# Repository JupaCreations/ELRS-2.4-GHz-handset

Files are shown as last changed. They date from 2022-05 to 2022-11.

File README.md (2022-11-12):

ELRS-2.4-GHz 2 channel CAR TX handset.



This project is a rework of the ergonomic handset which can be found here.

https://www.thingiverse.com/thing:4868117

I reworked the upper and lower cover to make it comply to the needs of a simple 2 channel CAR TX handset with EXPRESSLRS as carrier.

All switches are removed.

The original Jumper T-Lite hall gimbals are placed in a way that they can be adjusted in an angle that comforts the movement of the thumb.

Two screws accesable from the top of the transmitter can loosend or fastend at each gimbal to put it in a desired angled position.
There are two versions of gimbal clamps as Jumper redesigned the housing of the gimbals I found out.
"T-lite TX gimbal retainer V2" is for the gimbal versions that can not be clamped at the edges with the "T-lite TX gimbal retainer" version.

I put M3 thread in the mounting holes of the gimbals. Drill a 2.5 mm drill through them first than use a 3mm thread tapping tool with care.
The V2 version gimbal brackets are attached to the gimbal mounting holes with M3x8 mm screws.
The brackets are clamped down with a retainer that has a M3 nut pressed in, in combination with M3x20mm screws. 

As this is a 2 channel application the left gimbal is for throttle and the right gimbal for steering.
With the "T-lite TX gimbal blocker" you can block the up/down motion in the not used direction of the gimbal.

For the ELRS part a DIY 2.4 GHz SX1280 with special PCB is used. When you use a Jumper T-lite V2 ELRS version as donor transnmitter this extra board is obsolete.

PCB design https://oshwlab.com/jyesmith/expresslrs-jumper-t-lite

Video 1 https://www.youtube.com/watch?v=8L0xCDgLQ8s

Video 2 https://www.youtube.com/watch?v=rfa2Ir5jLuc

The upper and lower cover are printed in PLA.
The lower cover has 4 inserts fitted with the size of 4.2 x 5 mm for M3 to secure the upper with the lower cover with M3x16mm hexagon screws.

The battery is a single 18650 3.3 volt cell.

The original Jumper T-Lite electronics are taken from a new handset and fitted with the original (4) screws in the upper cover.
The 4 wire cable from the gimbals to the mainboard might be to short in some cases and need a longer version as the handset is wider.

The receiver is a Happy Model EP2 receiver which is mounted on a DIY carrier board with a 5 volt regulator and the servo pins.
There are pins available for 2 channels (throttle and steering) and for the timing transponder if you use it for racing events.
Alternatively you can also use this receiver.
https://www.mateksys.com/?portfolio=elrs-r24-p6



BOM

4 x M3 4.2x5mm brass inserts

4 x M3x8mm hexagon head screws

4 x M3x16mm hexagon head screws

4 x M3x20mm hexagon head screws

4 x M3 nut

2 x wire cable 15cm with JST 1.25mm 4Pin Female connector (if original cables are to short)

1 x Jumper T-Lite handset for the electronics and gimbals

1 x 3D printed parts in PLA or PETG filament

1 x DIY 2.4 GHz Express LRS TX board (Jumper T-Lite is now also in a ELRS ready version 2 available which makes this part obsolete)

1 x antenna connector from UFL-IPX to SMA connector 5 cm length (Jumper T-Lite is now also in a ELRS ready version 2 available which makes this part obsolete)

1 x antenna 2.5 GHz SMA connector (Jumper T-Lite is now also in a ELRS ready version 2 available which makes this part obsolete)

2 x spring steel 18650 battery contact

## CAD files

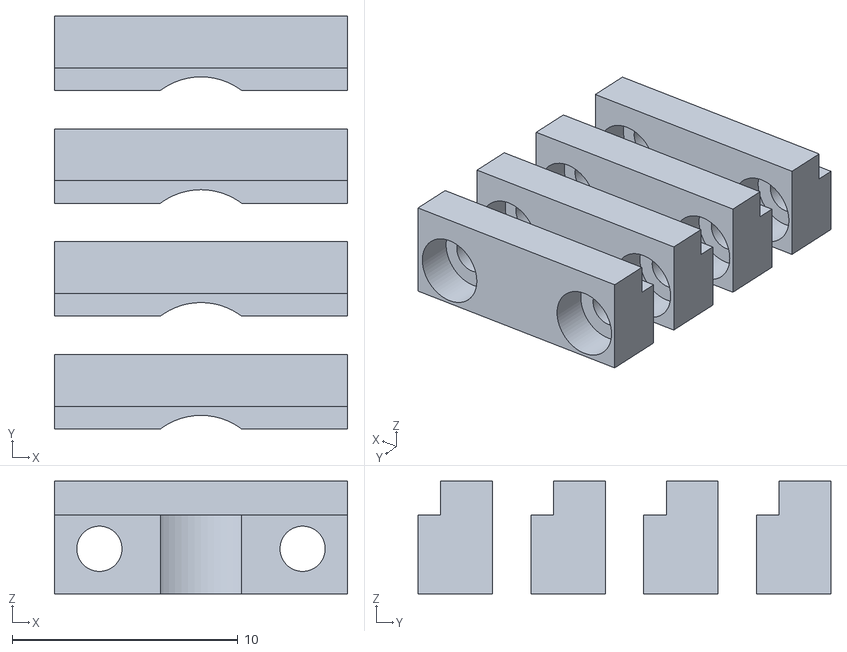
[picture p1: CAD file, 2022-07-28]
T-lite TX gimbal blocker.stl
13.0 x 18.3 x 5.00

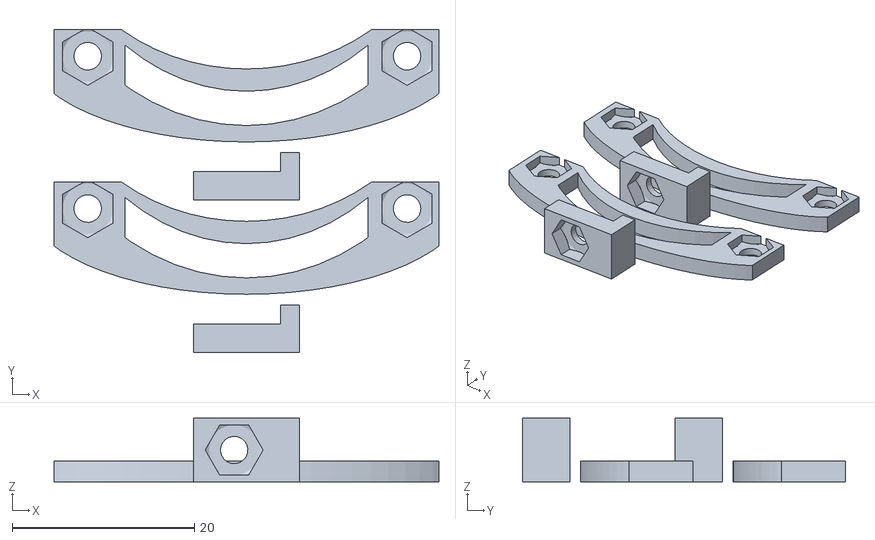
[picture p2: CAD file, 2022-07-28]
T-lite TX gimbal retainer V2.stl
42.2 x 35.4 x 7.00

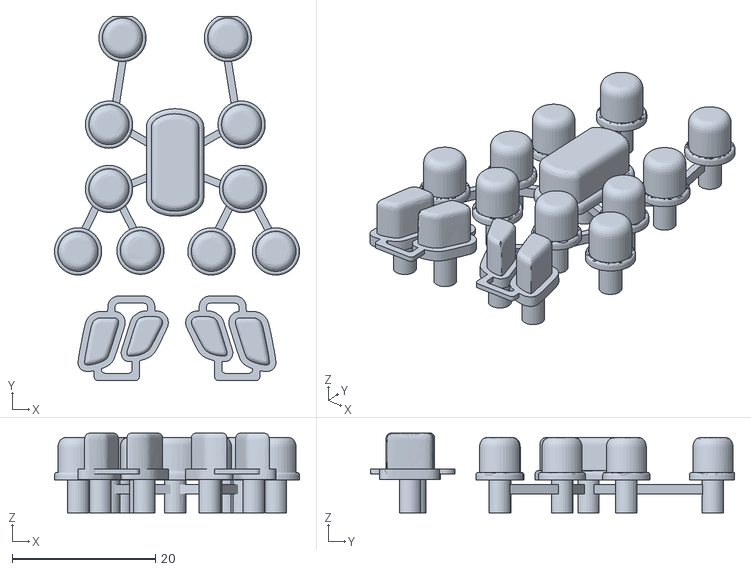
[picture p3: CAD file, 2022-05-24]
T-Lite TX buttons.stl
34.2 x 50.8 x 11.1

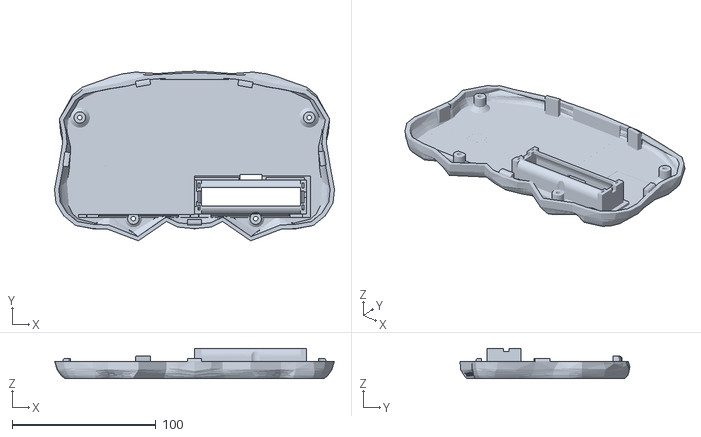
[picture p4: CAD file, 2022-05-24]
T-Lite TX lower cover.stl
194.6 x 117.9 x 21.0

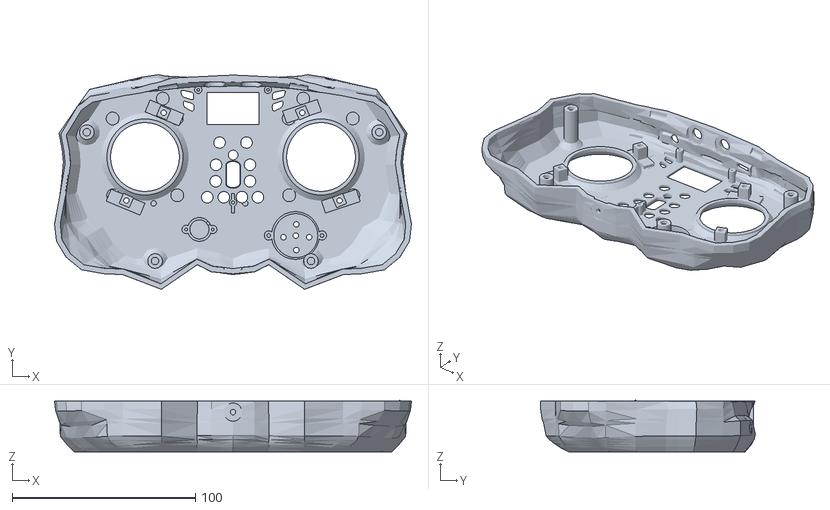
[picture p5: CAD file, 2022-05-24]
T-Lite TX upper cover.stl
194.7 x 117.1 x 28.3

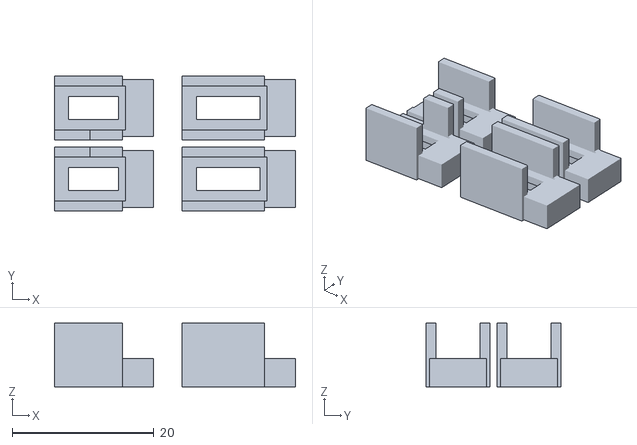
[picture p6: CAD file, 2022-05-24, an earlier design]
T-Lite TX gimbal retainer.stl
34.0 x 19.0 x 9.00
